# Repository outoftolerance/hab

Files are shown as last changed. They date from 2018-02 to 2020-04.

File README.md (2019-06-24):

# HAB
HAB is a High Altitude Balloon project designed with specific goals in mind.
 - Take a picture of the curvature of the earth
 - Take a picture of the earth and space
 - Learn new things through project research (atmosphere, weather, etc)
 - Develop engineering skills (Software and Electrical)

The code for this project is written in the Arduino language so that it is portable and easy to understand for other people who might want to create a similar project of their own, or extend the project in their own way.

# Hardware

## Microcontroller
For this project we use the `ATSAMD21G18A-U` Microcontroller, this is supported through the Arduino project as the Arduino Zero and through Adafruit as their Feather M0 board (as well as other variants available). We make use of the Adafruit version of the board support package as it allows more flexibility in terms of serial ports by not using the EDBG interface that is by default used by the Arduino Zero, instead it uses the USB interface.

We chose this specific microcontroller because it has a feature called SERCOM that allows for in-software definition of serial, I2C, and SPI interfaces using different pins. Since we have a large number of serial peripherals for this project (GPS, Radio, Cellular, APRS) we needed to be able to define more than the standard single serial port for an Arduino board. While it would be possible to define additional serial interfaces used the `SoftwareSerial` library, this is generally not good practice and has many implementation pitfalls.

Additionally, the chip is not very large. We had the option of using the `ATMEGA2560` (as used on the Arduino Mega board, which has four serial interfaces) however the physical size (and cost!) of that microcontroller is significantly larger in comarison. We also get other side benefits such as more program memory, and faster clock speed, that aren't NEEDED for this project but are a nice to have.

### SERCOM
We make use of the SERCOM feature of the micro by definig two additional serial ports beyond those already defined by default, no other customised use of the SERCOM system is needed for this project.

*Note that when adding serial port interfaces using SERCOM, the TX pin may only reside on either PAD0 or PAD2 of a specific SERCOM interface! This limits the available SERCOM interfaces that we can choose from because some pads are being used for other interfaces (like I2C or SPI).*

The following table shows the pinout for the `ATSAMD21G18A-U` SERCOM and the uses that we are making of these pins for the project. This table was sourced from ADafruit's fantastic guide on using the Feather M0 that can be [found on their website](https://learn.adafruit.com/using-atsamd21-sercom-to-add-more-spi-i2c-serial-ports/overview).

|Microcontroller Pin|Arduino 'Pin'|SERCOM|SERCOM alt|Configured Interface|
|---|---|---|---|--|
|PA00|Used by xtal|SERCOM1.0|||
|PA01|Used by xtal|SERCOM1.1|||
|PB08|A1|SERCOM4.0|||
|PB09|A2|SERCOM4.1|||
|PA04|A3|SERCOM0.0|||
|PA05|A4|SERCOM0.1|||
|PA06|D8|SERCOM0.2|||
|PA07|D9|SERCOM0.3|||
|PA08|D4|SERCOM0.0|SERCOM2.0|Serial3 - Cellular|
|PA09|D3|SERCOM0.1|SERCOM2.1|Serial3 - Cellular|
|PA10|D1|SERCOM0.2|SERCOM2.2|Serial1 - GPS|
|PA11|D0|SERCOM0.3|SERCOM2.3|Serial1 - GPS|
|PB10|D23 / MOSI|SERCOM4.2||SPI - MicroSD|
|PB11|D24 / SCK|SERCOM4.3||SPI - MicroSD|
|PA12|D22 / MISO|SERCOM2.0|SERCOM4.0|SPI - MicroSD|
|PA13|Used by EDBC|SERCOM2.1|SERCOM4.1||
|PA14|D2|SERCOM2.2|SERCOM4.2||
|PA15|D5|SERCOM2.3|SERCOM4.3||
|PA16|D11|SERCOM1.0|SERCOM3.0|Serial2 - Radio|
|PA17|D13|SERCOM1.1|SERCOM3.1||
|PA18|D10|SERCOM1.2|SERCOM3.2|Serial2 - Radio|
|PA19|D12|SERCOM1.3|SERCOM3.3||
|PA20|D6|SERCOM5.2|SERCOM3.2||
|PA21|D7|SERCOM5.3|SERCOM3.3||
|PA22|D20 / SDA|SERCOM3.0|SERCOM5.0|I2C - Sensors|
|PA23|D21 / SCL|SERCOM3.1|SERCOM5.1|I2C - Sensors|
|PA24|Used by USB|SERCOM3.2|SERCOM5.2|Serial - Debug|
|PA25|Used by USB|SERCOM3.3|SERCOM5.3|Serial - Debug|
|PB22|D30 / EDBG TX|SERCOM5.2||Serial5 - APRS|
|PB23|D31 / EDBG RX|SERCOM5.3||Serial5 - APRS|
|PA30|Used by SWCLK|SERCOM1.2|||
|PA31|Used by SWDIO|SERCOM1.3|||
|PB02|A5|SERCOM5.0|||
|PB03|D25 / RX LED|SERCOM5.1|||

## Communications
Communications is one of the major difficulties when designing a High Altitude Balloon because of the distances that it has to travel and the fact that the system needs to be recovered at a random, unknown, future location (or you lose all your hard work!). For this reason, there are multiple redundant communications interfaces that have been designed into the vehicle.

### Packet Radio
The first, and simplest, form of communication between the vehicle and us on the ground is a packet radio. Essentially this works as a serial port over radio waves and allows data to be passed from the vehicle to the ground (such as position information) as well as allowing commands to be send to the vehicle during operation.

We chose an [RFD900+ radio modem](http://store.rfdesign.com.au/rfd-900p-modem/) for this project, it is well known within the drone industry as a reliable and well-performing radio that can be configured and paired with different antenna systems to provide exceptional range.

This communications interface will be used to communicate the following information:
- Telemetry from vehicle
- Position from vehicle
- Events from vehicle
- Commands to vehicle

### Cellular
Secondly we will use a cellular modem to send and receive data from the ground to the vehicle. This method is not reliable as a tracking system for the vehicle throughtout the flight, however is robust at low altitudes within cellular network reception range. It is also a flexible interface, it can either send text messages to us, or data over the internet, or a combination of both!

The reason we added this radio was as a backup in-case the other tracking systems fail, or when at low altitudes, radio signals from the other two methods are obscured by terrain or ground objects where the balloon lands. The cellular connection should be able to text message us with the location of the vehicle at low altitudes and when at rest.

The communucations interface will be used to communicate the following information:
- Position from the vehicle
- Events from the vehicle

### APRS
An APRS (Automatic Packet Reporting System) radio has also been added, this allows for the tracking of the balloon through the HAM radio APRS network of receivers, and potentially from our own receiver. The system is very limited in terms of how frequently data can be transmitted and how much data can be transmitted at a time, however it is very very long range and is well supported as a method of tracking vehicles. 

We chose the [MicroTrak 2000](https://drive.google.com/open?id=1uPaUfZ47ibVQPEURd_sj6lUmIUkslmQF) APRS transmitter from Byonics for this project because of its small form-factor, high power, and easy integration into our custom electical and mechanical design. This model is no longer in production and has been superceded by an even smaller form-factor device, the MicroTrak 2001.

This communications interface will be used to communicate the following information:
- Position from the vehicle

## Sensors
There are some sensors needed for basic functionality of the balloon (such as a GPS receiver) and others are just for fun!

### GPS
A GPS receiver is a basic requirement for being able to position the vehicle and track it during its mission. We chose a basic off-the-shelf GPS receiver from Adafruit that has been used in high altitude balloon projects with success in the past, the [Adafruit GPS V3](https://www.adafruit.com/product/746).

### IMU
An IMU is added to give basic orentation information, as well as being able to detect freefall and other events such as touchdown. We chose a simple all-in-one IMU board, the [Adafruit 10DOF](https://www.adafruit.com/product/1604). This is no longer available but still functions great and we already had one.

### Atmospheric
None of these sensors are really neded, however the data they produce is fun to look at after the flight and get an idea of the make-up of our atmosphere! We chose to add temperature, humidity, and gas sensors to the project, the specific models and boards haven't been defined yet but will come.

## Interconnects
The different elements of the system are connected together using Serial, I2C, and SPI interfaces, as well as a few GPIO used for some smaller peripherals. The folliwing diagram shows how each element of the system is connected.

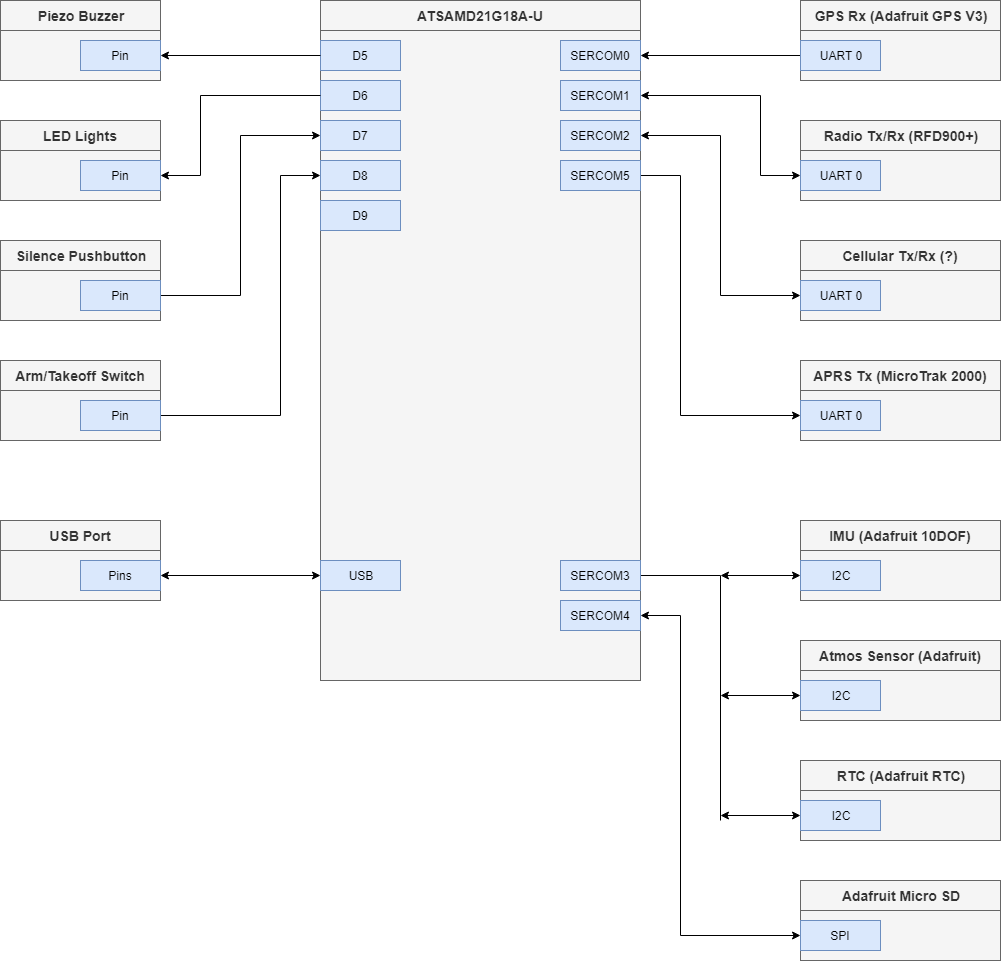
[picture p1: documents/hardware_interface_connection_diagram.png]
Hardware Interface Connection Diagram


# Software
The software for this project is likely to be much more complex than is really required for such a simple mission, however part of the goal of this project was to learn new techniques and to advance my knowledge of object-oriented programming, abstraction, division of responsibility, and writing extensible and maintainable code. 

For this reason different sub-systems are built into their own libraries, these libraries are described at a functional level here, and at a technical level in the header file comments for each package.

## Mission States
In order to control the different functions of the balloon at different stages in the flight, a state machine was developed which tracks mission state based on inputs such as telemetry, button presses, and command messages.

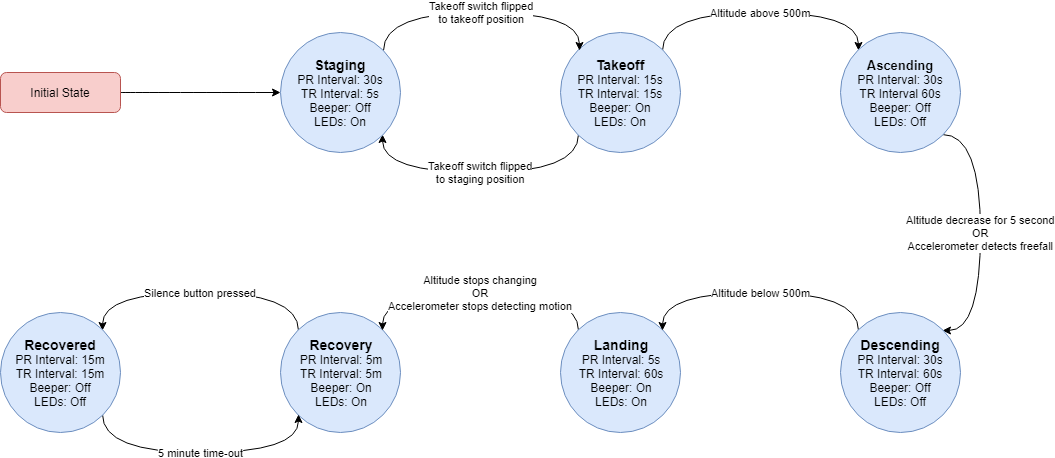
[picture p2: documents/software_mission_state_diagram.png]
Mission State Diagram


### State Descriptions

**Staging:** While waiting to launch and on the ground, used to prepare the vehicle and sub-systems.

**Takeoff:** Once ready to takeoff and all staging work has been completed this state is engaged manually.

**Ascending:** Once takeoff has completed and the vehicle is ascending in altitude.

**Descending:** Once ascension has completed and descent has started.

**Landing:** When vehicle is about to land and has descended almost to the ground.

**Receovery:** Once touchdown has been detected and the vehicle is waiting for recovery.

**Receovered:** When recovery has been detected but power-off is pending.

### State Table

|State|Configuration|Entrance Condititions|Exit Conditions|
|-----|---|---|---|
|Staging |<ul><li>Telemetry Reporting Frequency: 1/5 Hz</li><li>Telemetry Logging Frequency: 1/5 Hz</li><li>Position Reporting Frequency: 1/30 Hz</li><li>LEDs: On</li><li>Beeper: Off</li></ul>|<ul><li>State is set by default at boot.</li><li>Launch switch is flipped to staging and current mission state is `Takeoff`.</li></ul>|<ul><li>Launch switch is flipped to `Takeoff` from `Staging`.</li></ul>|
|Takeoff |<ul><li>Telemetry Reporting Frequency: 1/15 Hz</li><li>Telemetry Logging Frequency: 1/5 Hz</li><li>Position Reporting Frequency: 1/15 Hz</li><li>LEDs: On</li><li>Beeper: On</li></ul>|<ul><li>Launch switch is flipped to `Takeoff` from `Staging`.</li></ul>|<ul><li>Launch switch is flipped to `Staging` from `Takeoff`.</li><li>Altitude increases above 500m.</li></ul>|
|Ascending |<ul><li>Telemetry Reporting Frequency: 1/60 Hz</li><li>Telemetry Logging Frequency: 1/5 Hz</li><li>Position Reporting Frequency: 1/30 Hz</li><li>LEDs: Off</li><li>Beeper: Off</li></ul>|<ul><li>Altitude increases above 500m.</li></ul>|<ul><li>Accelerometer detects freefall or altitude starts dropping for 5 consecutive seconds.</li></ul>|
|Descending|<ul><li>Telemetry Reporting Frequency: 1/60 Hz</li><li>Telemetry Logging Frequency: 1/5 Hz</li><li>Position Reporting Frequency: 1/30 Hz</li><li>LEDs: Off</li><li>Beeper: Off</li></ul>|<ul><li>Accelerometer detects freefall or altitude starts dropping for 5 consecutive seconds.</li></ul>|<ul><li>Altitude decreases below 500m.</li></ul>|
|Landing |<ul><li>Telemetry Reporting Frequency: 1/60 Hz</li><li>Telemetry Logging Frequency: 1/5 Hz</li><li>Position Reporting Frequency: 1/5 Hz</li><li>LEDs: On</li><li>Beeper: On</li></ul>|<ul><li>Altitude decreases below 500m.</li></ul>|<ul><li>Accelerometer stops detecting motion or altitude stops changing for 5 consecutive seconds.</li></ul>|
|Recovery  |<ul><li>Telemetry Reporting Frequency: 1/300 Hz</li><li>Telemetry Logging Frequency: 1/5 Hz</li><li>Position Reporting Frequency: 1/300 Hz</li><li>LEDs: On</li><li>Beeper: On</li></ul>|<ul><li>Accelerometer stops detecting motion or altitude stops changing for 5 consecutive seconds.</li><li>After waiting 5 minutes in Recovered mode.</li></ul>|<ul><li>Silence button is pressed.</li></ul>|
|Recovered |<ul><li>Telemetry Reporting Frequency: 1/300 Hz</li><li>Telemetry Logging Frequency: 1/5 Hz</li><li>Position Reporting Frequency: 1/300 Hz</li><li>LEDs: Off</li><li>Beeper: Off</li></ul>|<ul><li>Silence button is pressed.</li></ul>|<ul><li>After waiting 5 minutes in Recovered mode.</li></ul>|

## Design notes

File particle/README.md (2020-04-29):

# particle

A Particle project named particle

## Welcome to your project!

Every new Particle project is composed of 3 important elements that you'll see have been created in your project directory for particle.

#### ```/src``` folder:  
This is the source folder that contains the firmware files for your project. It should *not* be renamed. 
Anything that is in this folder when you compile your project will be sent to our compile service and compiled into a firmware binary for the Particle device that you have targeted.

If your application contains multiple files, they should all be included in the `src` folder. If your firmware depends on Particle libraries, those dependencies are specified in the `project.properties` file referenced below.

#### ```.ino``` file:
This file is the firmware that will run as the primary application on your Particle device. It contains a `setup()` and `loop()` function, and can be written in Wiring or C/C++. For more information about using the Particle firmware API to create firmware for your Particle device, refer to the [Firmware Reference](https://docs.particle.io/reference/firmware/) section of the Particle documentation.

#### ```project.properties``` file:  
This is the file that specifies the name and version number of the libraries that your project depends on. Dependencies are added automatically to your `project.properties` file when you add a library to a project using the `particle library add` command in the CLI or add a library in the Desktop IDE.

## Adding additional files to your project

#### Projects with multiple sources
If you would like add additional files to your application, they should be added to the `/src` folder. All files in the `/src` folder will be sent to the Particle Cloud to produce a compiled binary.

#### Projects with external libraries
If your project includes a library that has not been registered in the Particle libraries system, you should create a new folder named `/lib/<libraryname>/src` under `/<project dir>` and add the `.h`, `.cpp` & `library.properties` files for your library there. Read the [Firmware Libraries guide](https://docs.particle.io/guide/tools-and-features/libraries/) for more details on how to develop libraries. Note that all contents of the `/lib` folder and subfolders will also be sent to the Cloud for compilation.

## Compiling your project

When you're ready to compile your project, make sure you have the correct Particle device target selected and run `particle compile <platform>` in the CLI or click the Compile button in the Desktop IDE. The following files in your project folder will be sent to the compile service:

- Everything in the `/src` folder, including your `.ino` application file
- The `project.properties` file for your project
- Any libraries stored under `lib/<libraryname>/src`

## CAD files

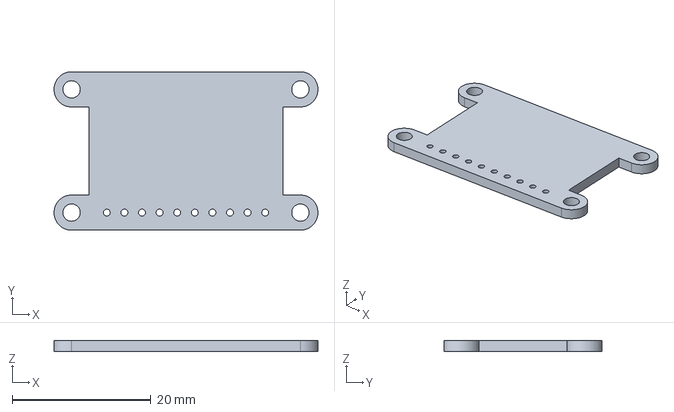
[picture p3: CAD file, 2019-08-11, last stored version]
hardware/00_RROJECT_RESEARCH/3D Models/Adafuit_10DOF.step
38.1 x 22.9 x 1.62 mm

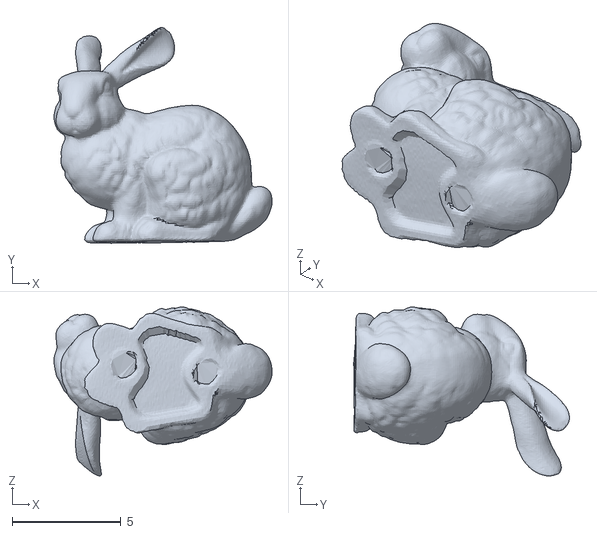
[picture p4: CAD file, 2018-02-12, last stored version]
include/Adafruit_10DOF/ahrs/processing/cuberotate/data/bunny.obj
10.0 x 9.94 x 7.77

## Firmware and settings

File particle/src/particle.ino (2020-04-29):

/*
 * Project particle
 * Description:
 * Author:
 * Date:
 */

// setup() runs once, when the device is first turned on.
void setup() {
  // Put initialization like pinMode and begin functions here.

}

// loop() runs over and over again, as quickly as it can execute.
void loop() {
  // The core of your code will likely live here.

}

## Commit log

2018-02-12 Added Adafruit sensor libraries for 10 DOF board
    [bunny.obj]
2018-06-14 Code fixes
    Fixed code syntax errors and comments
    [hab.ino]
2018-06-14 Syntax and linking fixes
    [hab.ino]
2018-06-15 Fixed compiler issues
    - Moved libraries to correct folder
    - Changed include statements
    - Fixed code errors
    - Compiles now!
    [hab.ino]
2018-08-21 Updates
    - Added Buffer class
    - Created gps char buffer within telemetr
    - Fixed logging issues with const type
    - Created Radio.h, started making this abstraction
    Next:
    - Get GPS char buffer and push to APRS serial port
    - Define a messaging interface for other radio interfaces
    - Open interface to RFD900 serial port
    - Integration SMS messaging with celular
    [hab.ino]
2019-02-09 Lots of development
    - HDLC Library
    - Timer Library
    - CRC Library
    - Compiles now
2019-05-11 Updates to structure
    - Improved state machine (event driven)
    - Fixed a lot of compile issues (more still exist)
    - Used higher abstraction for stream interfaces
    - Added a readme
    - Renamed a few methods
    - Added a hardware configuration header to clean up main program file
    [hab.ino]
2019-05-18 Fixes all compile errors and warnings
    [hab.ino]
2019-05-18 Corrects mission states enum naming
    [hab.ino]
2019-05-18 Implements sendTelemetryReport and fixes Telemetry library to pass by reference
    [hab.ino]
2019-05-18 Corrects M0 compile errors
    [hab.ino]
2019-05-19 Adds datasheet pin references to comments
2019-05-19 Adds basic sensor documentation
2019-05-21 Updates to support M0 and bug fixes
    [hab.ino]
2019-05-21 Adds led and buzzer
    [hab.ino]
2019-05-25 Updates to GPS and logging
    IMU and GPS tested and working
2019-06-03 Fixes SD card data logging
    [hab.ino]
2019-06-04 Adds RTC and functionality
    - Adds RTC library for Adafruit precision RTC
    - Adds ability to detect and update RTC power loss
    - Will auto update RTC from GPS after power loss
2019-06-09 Fix bugs in timing addition
    [hab.ino]
2019-06-12 Makes RTC optional for logging
    - Overloaded constructor
    - Changed RTC to pointer from reference (since it has to be NULL sometimes)
    - Use milliseconds since program start for timing if no RTC is given
2019-06-13 Added hardware directory and associated files
    [HAB_V01R01.PcbDoc, HAB_V01R01.PrjPCB, [01] - COVER PAGE.SchDoc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]
2019-06-14 Adds execution blinky LED using timer instead of delay
2019-06-14 timer start code
2019-08-11 initial schematic and PCB layout
    [Adafuit_10DOF.step, HAB_V01R01.PcbDoc, HAB_V01R01.PrjPCB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]
2019-08-11 changed project title in schematics
    [[01] - COVER PAGE.SchDoc, [02] - HAB.SchDoc, [03] - HELPFUL INFO.SchDoc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]
2019-10-19 Correct many bugs!
    - Fix main loop execution timers
    - Fix init problems and add additional device checking
    - Pass structs and strings by reference instead of raw pointers
    - Correct logging issues with preamble date not printing
    - Pass inputs as const for many functions
    [hab.ino]
2019-10-27 Add many debug outputs and fix issues with control flow for mission state
    [hab.ino]
2019-10-27 Fix heartbeat length bug
    [hab.ino]
2019-10-27 Fixed message sending bug
    [hab.ino]
2019-12-15 Add velocity to telemetry
2020-05-04 Fixes support for LED in code to PWM servo signal (for Flytron LEDs)
    [hab.ino]
2020-05-11 Updates to support fixes and changes to messaging
    [hab.ino]
2020-05-21 Removed hardware files and updated to latest tinygps
    [Adafuit_10DOF.step, HAB_V01R01.PcbDoc, HAB_V01R01.PrjPCB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]
2020-05-27 Updated buzzer and strobe for Icarus board
    [hab.ino]

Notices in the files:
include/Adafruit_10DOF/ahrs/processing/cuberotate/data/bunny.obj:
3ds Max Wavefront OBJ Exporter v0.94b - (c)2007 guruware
